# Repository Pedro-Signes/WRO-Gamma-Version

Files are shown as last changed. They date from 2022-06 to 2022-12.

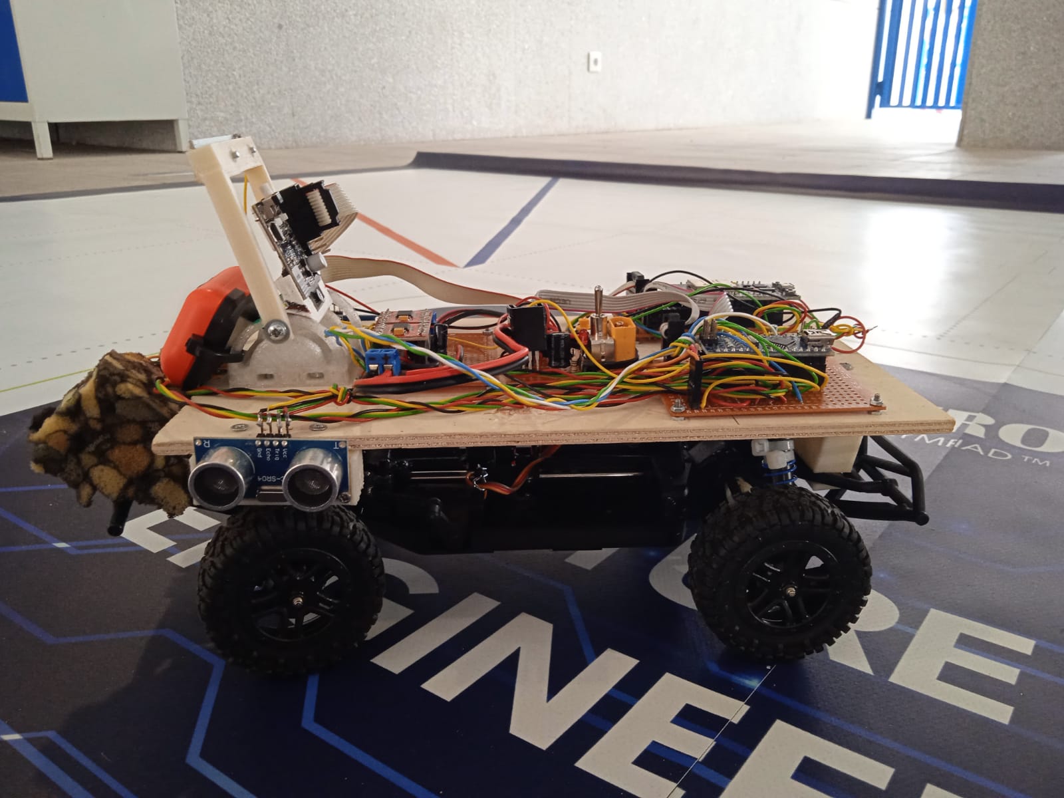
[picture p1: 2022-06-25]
vehicle-photos/FotoCocheIzquierda.jpeg

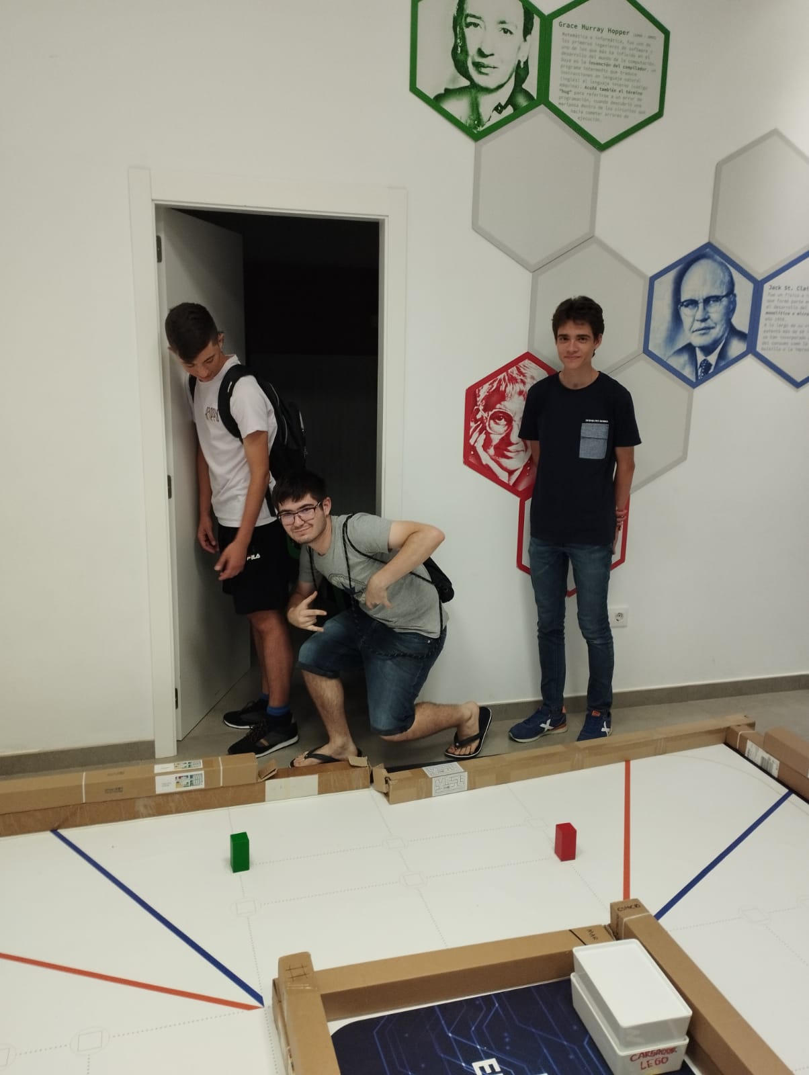
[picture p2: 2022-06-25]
team-photos/FotoGraciosa.jpeg

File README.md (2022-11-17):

# WRO-Gamma-Version
Diseño coche autónomo para la competición Future Engineers 2022
* Equipo: GammaVersion 
* Nombre del Coche: Mototruco
* Integrantes:
  * Javier Calero
  * Pablo Huertas
  * Pedro Signes

Nuestro equipo proviene de la cuidad de Denia (Alicante), y se compone de tres integrantes más un coach de la academia Diverbot, la cual también es la sede donde hacemos todas las pruebas con el robot.

A la hora de hablar del robot, tenemos que destacar los dos microcontroladores que tenemos, los cuales se comunican por un puerto I2C en un sistema maestro (ESP32) esclavo (Arduino Nano).No obstante nuestro robot contiene adicionalmente una cámara inteligente Pixy 2.0, la cual facilita mucho el trabajo a la hora de detectar los obstáculos y se comunica con el ESP32 mediante un puerto SPI.

Volviendo a los microcontroladores, el ESP32 a la hora de comunicarse con el Arduino Nano puede hacer dos cosas, preguntarle o ordenarle, puesto que el Arduino Nano es el esclavo de este sistema cuando reciba una de estas dos hará lo siguiente, responderá a la pregunta o hará la orden.

Metiéndonos más en detalle, el ESP32 contiene en su código una maquina de estados, la cual dependiendo de qué información reciba del Arduino Nano. No obstante, el ESP 32 no solo recibe información del Arduino Nano, también de la cámara, la cual al ser inteligente se puede programar para que nos mande un mensaje cuando vea un bloque, y de que color es.

Pasando al Arduino Nano, este está conectado al todo al motor, al servo, a los ultrasonidos, a un giroscopio, y a un encoder. Mientras esta esperando a los mensajes del ESP32 el Arduino Nano mantiene la brujula del coche funcionando y regula la velocidad a la indicada gracias a un DP programado.

Después cabe destacar la Pixy 2.0, la cual ya tiene un programa para detectar objetos y sus colores. No obstante, la cámara se le tiene que indicar unos parámetros en forma de asignaciones, que luego recibirá el ESP32 y con ellas puede tomar las decisiones. 

Por ultimo cabe destacar los cuatro ultrasonidos que posee el robot, ya que estos le indica la distancia que tiene delante, a los lados, y detrás. Esto datos llegaran al ESP32 mediante el sistema explicado previamente, y con ellos el ESP32 tomara diferentes decisiones.

Versión en Inglés/English Version

Autonomous car design for the Future Engineers competition 2022

* Team: GammaVersion 
* Name of the car: Mototruco
* Members:
  * Javier Calero
  * Pablo Huertas
  * Pedro Signes

Our team comes from the city of Denia (Valencian region, Spain), and the team is made up of three members (Pablo, Pedro & Javi) plus a coach from the Diverbot academy, which is also the headquarters where we do all the developement of the project. We met on February of this year and we have been working hard since then to succeed in accomplish the chellenge of the Future Engineers Category of the World Robot Olympiad 2022.

The base of our robot is the chassis of a radio control car that we have broke down. Therefore, we alredy have a structure, an engine and a servo-direction. To achieve the car being autonomous we have to add a microcontroller, for this job we decided at the begining to use a Arduino Uno. This has been changed in june to an ESP32 and an Arduino Nano because only one microcontroller was not enough to opperate all the program with the adequate accuracy. This paradigma has been used in the Madrid competition and in the national final, but two weeks ago we ran away of interrupt pins, so we added an Arduino Nano Every since all its pins have interruptions. To support these three microcontrollers we have designed a wooden plank, where later we would place all the electronics. To join the plank with the chassis we have designed a couple of 3D supports, a frontal wall and two lateral pillars.

Our car is divided in four parts: the structure, explained before; the microcontrollers, which run the program; the sensors and the engine and servos.
The main part of our robot is the three controllers each one with a different program running. These programs are not parallel or isolated, they communicate trough an I2C bus. This protocol consists on a master, who can ruequest or send data to a slave who obeys the orders of the master. In our case, the ESP32 is the master, and the Arduino Nano and the Arduino Nano Every are the slaves.

By using this protocol we enable the ESP32 to run the main program at a good pace. The ESP32 has a little state machine, which time ago was huge but we have been able to simplify it by the algorithm we have developed, which is going to be explained now. The function of the main program is to detect the color blocks and pass them by the correct side. The way we have done it is by calculating the position of the car, x and y coordinates (width and length, respectively), at every time and telling the car to go to certain X position, which will be right or left. The knowledge of the position can be achieved by integrating the distance and the angle of the car at every time with a certain trigonometric function. An encoder is used to know the position and an MPU 9250 to work out the angle. The encoder has been designed with the 3D printer with 8 holes to let the light pass trough and it has been connected to the Arduino Nano. The MPU has a gyroscope mode, which lets you know the angular speed of the car, and integrating the angular speed over time you calculate the angle at which the car is respect to the origin. Let us point that the MPU is also connected to the ESP32 by a I2C bus, but in a different port to the employed with the arduinos because it caused problems.

In reference to the algorithm to manage the car going to a specific coordinate, it is based in a PID controller, however only the P and D terms. The desired setpoint is the objective position, the variable to control is the position and the actuator is the direction servo. The error between the desired setpoint and the actual value of the variable is worked out and the proportional and derivative are aplied. The result of the calculations is the angle at which the car has to point to arrive to the desired position.

To keep the algorithm symetric in every section we reset the coordinate system, hence, to avoid a red block the car will always have to move 20 cm from the origin, the center of the section. This change of coordinates can be done by a simple mathematical opertaion or taking into account the distance to the walls.

Restarting the coordinate system and employing the PD controller of the position the turns are consequently genereated, because when the coordiante system changes the car will still try to be at the desired X coordinate and in order to magange this it will move the servo and turn. The only thing we have to do is to set at which position it has to start to turn.

Moving on to the Arduino Nano, it is connected to the whole motor, servo, ultrasonics, and encoder. While it is waiting for messages from ESP32 the Arduino uno keeps the car in the last indicated speed thanks to a programmed DP.

Then it is worth highlighting the Pixy 2.0, an intelligent Pixy 2.0 camera, which greatly facilitates the work when detecting obstacles. Pixy already has a software to detect objects and their colors. To return the data, the camera has to be configured in the form of assignments, which the ESP32 will then receive and with them it can make decisions.

Finally, it is worth mentioning the four ultrasounds that the robot poses, since these indicate the distance that it has in front, to the sides, and behind. This sensors are connected to the Arduino Nano but the data will reach the ESP32 through the system explained previously, and with it the ESP32 will make different decisions. Recently we have noticed that the ultrasonic sensors would not obtain enough accurate measures of the distance and this affects our program beacause we cannot have an accurate check of the position of the car. Therefore we decided to add new sensors, the TOF sensors or unofficialy laser sensors. These ones are connected to the Arduino Nano Every because as explained before, all the pins in this microcontroller have interruptions which allow us to measure better with this sensors.

This is all our car, which we have developed with hard work and effort, but learning a lot.

FotoEquipo

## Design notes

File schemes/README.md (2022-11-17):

The schematics of the electromechanical components are in the electronics folder.

Aquí está el esquema de los componentes electromecánicos que han sido usados en el vehículo y de cómo se conectan entre ellos.

El esquemaico actual es el Circuito 2.1.

The current schematic is Circuito 2.1.

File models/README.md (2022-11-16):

In this folder the 3D models used in our project can be found.

En esta carpeta tiene los modelos usados para imprimir las piezas en la imporesora 3D.

Los modelos están diseñados e Freecad, herramienra libre para diseño 3D, en las carpetas de los diferentes diseños se encuentran los archivos de edición de dicho programa, para visualizar los modelos, dentro de las carpetas "stl" se encuentran los ficheros .stl.

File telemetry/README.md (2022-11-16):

This folder may be neglected since it only contains a record of the telemetry data of some tests we have done.
The Wifi_reader file is an old python program to receive the data the ESP32 sent via Wifi.

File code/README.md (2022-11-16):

All the code used in our project is stored in this folder.

En esta carpeta se encuentra todo el código usado en el proyecto.

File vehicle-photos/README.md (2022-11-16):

In this folder you may find two car photos's folders.
The New Car folder is that of the new version of the car, which will be used in the International Final.

En esta carpeta se encuentran las 6 fotos de las 6 caras del coche.

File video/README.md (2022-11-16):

The folder New Url contains the url to the updated version of the car review video on YouTube. (16/11/2022)
The Old Url is obsolete since it shows an older version of the car.

En este directorio está el archivo que contiene el link al video que muestra el coche conduciendo de manera autónoma.

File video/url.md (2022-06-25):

URL al video de Youtube del coche moviendose de forma autónoma
https://youtu.be/MbsSwNEmdMk

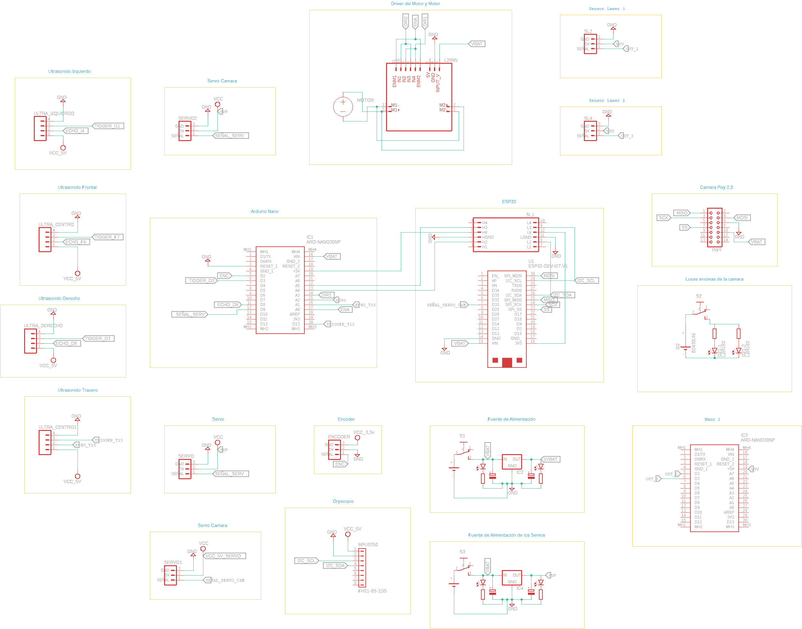
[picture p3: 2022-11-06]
schemes/electronics/Circuito/Circuito.png

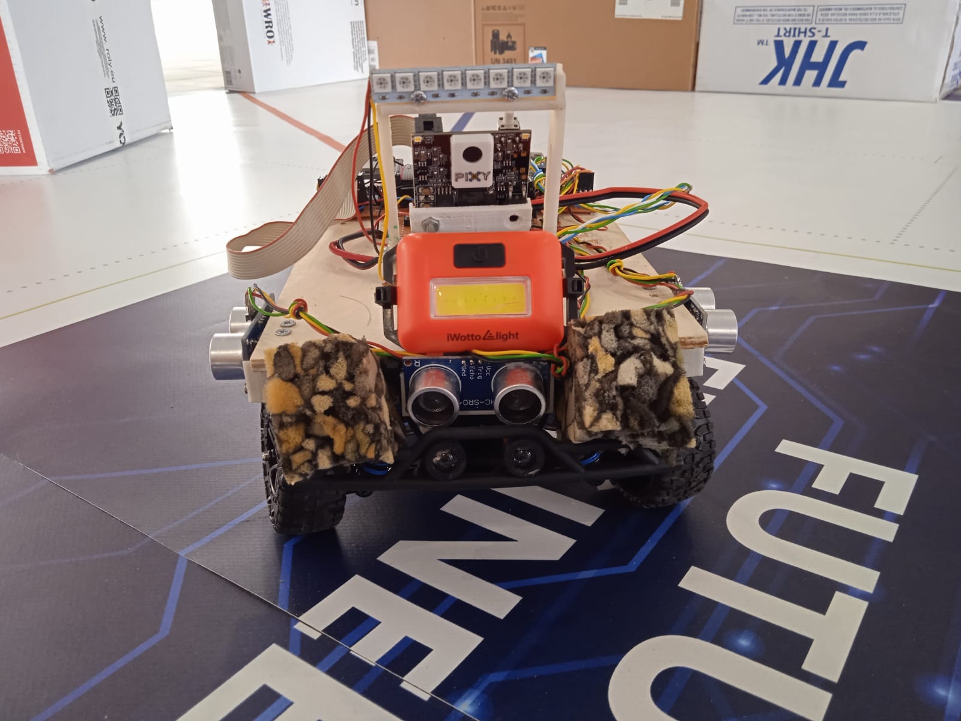
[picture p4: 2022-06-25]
vehicle-photos/FotoCocheDelante.jpeg

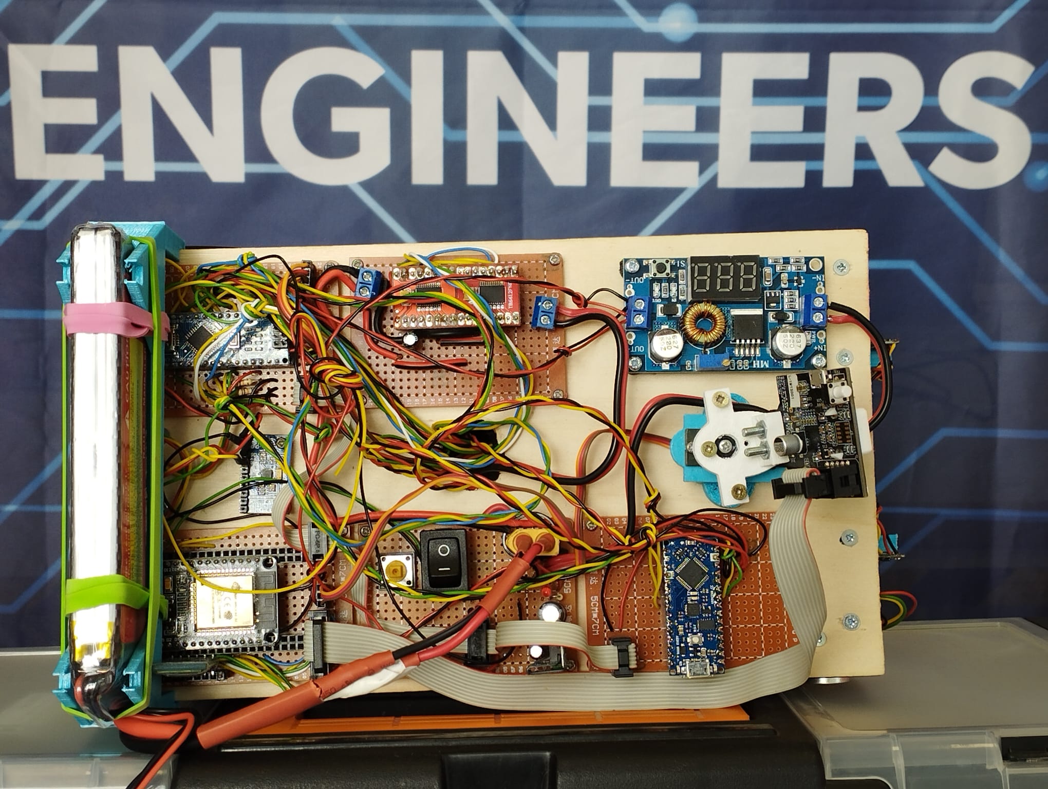
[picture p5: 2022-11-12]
vehicle-photos/New Car/FotoCocheArriba.jpg.jpeg

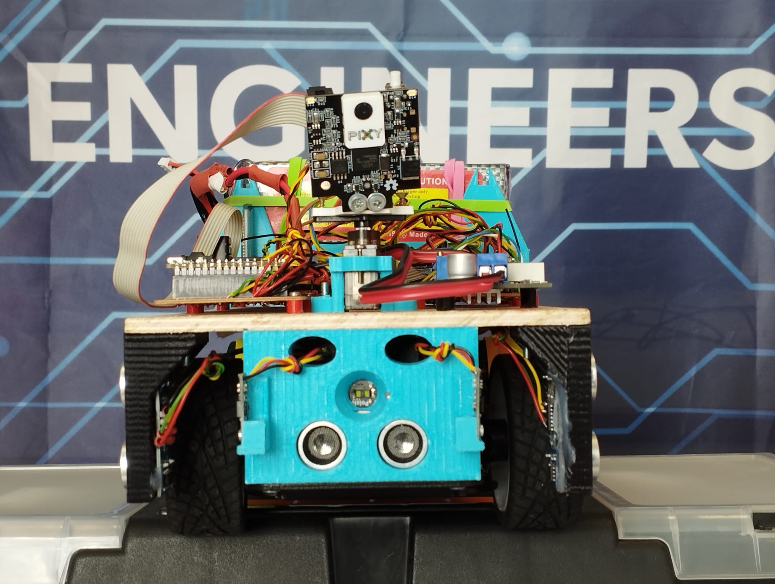
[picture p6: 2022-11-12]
vehicle-photos/New Car/FotoCocheDelante.jpg.jpeg

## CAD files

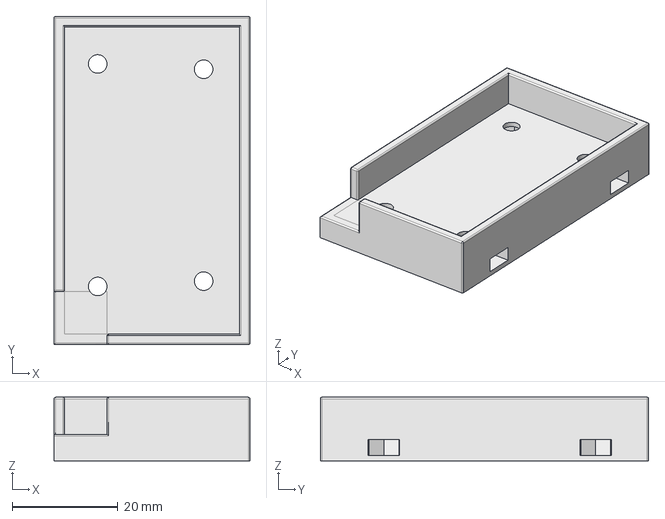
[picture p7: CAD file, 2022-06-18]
models/Soporte bateria/Soporte Bateria.FCStd
37.0 x 62.0 x 12.0 mm

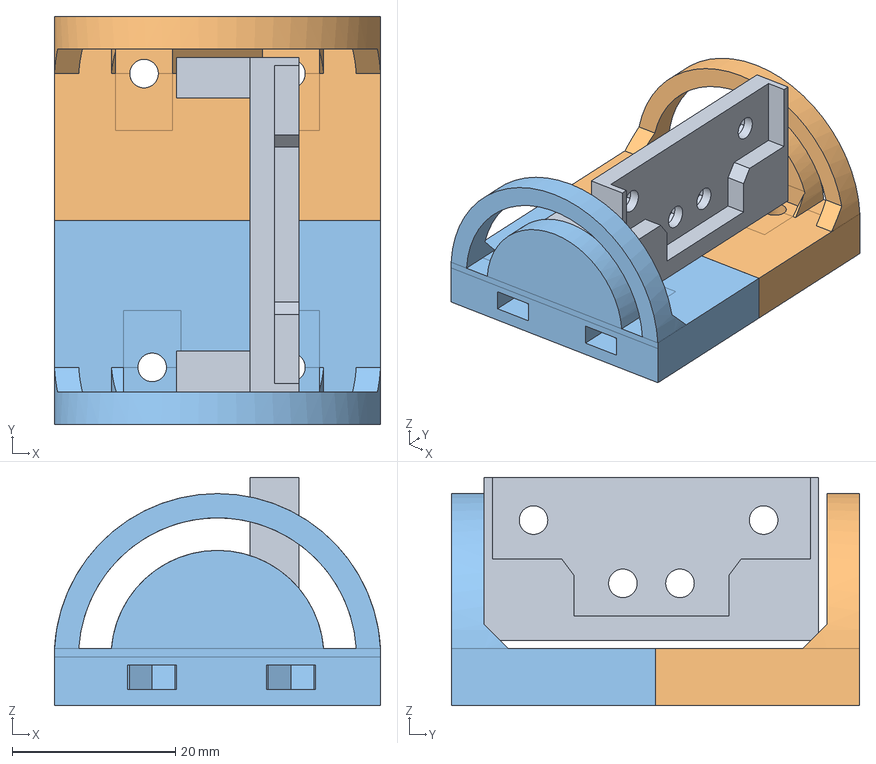
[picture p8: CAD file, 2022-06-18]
models/Soporte Camara/Soporte camara.FCStd
40.0 x 50.0 x 28.0 mm

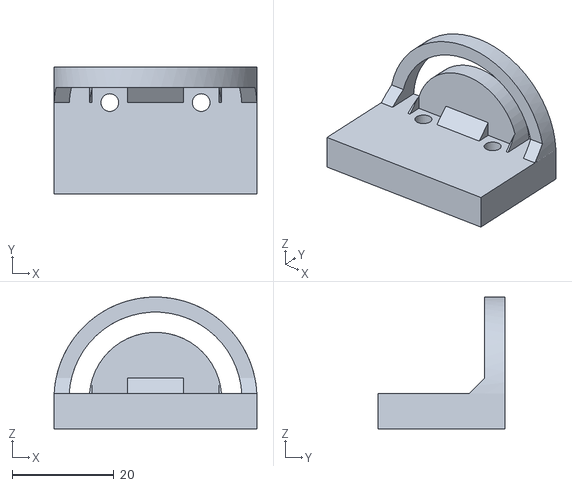
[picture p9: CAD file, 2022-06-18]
models/Soporte Camara/stl/Soporte camara 1.0/Soporte camara-Base1.stl
40.0 x 25.0 x 26.0

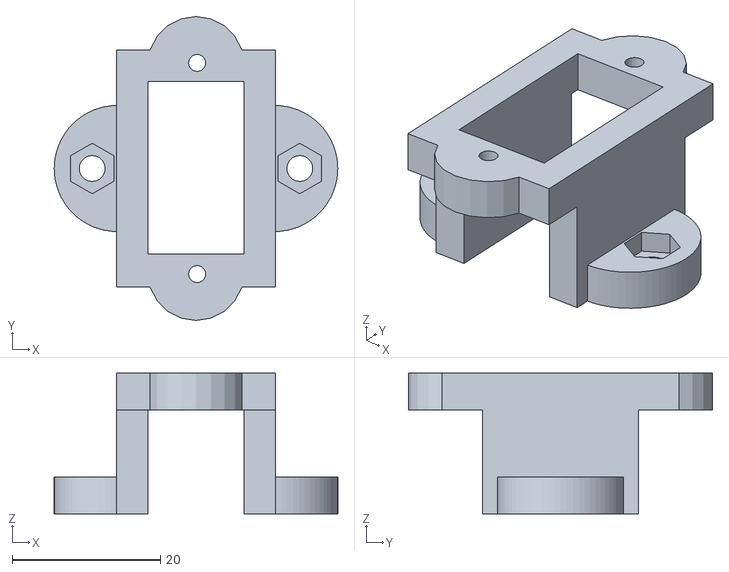
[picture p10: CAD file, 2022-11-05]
models/Soporte Camara/stl/Soporte camara 2.0/Soporte camara - Base servo.stl
38.2 x 41.0 x 19.0

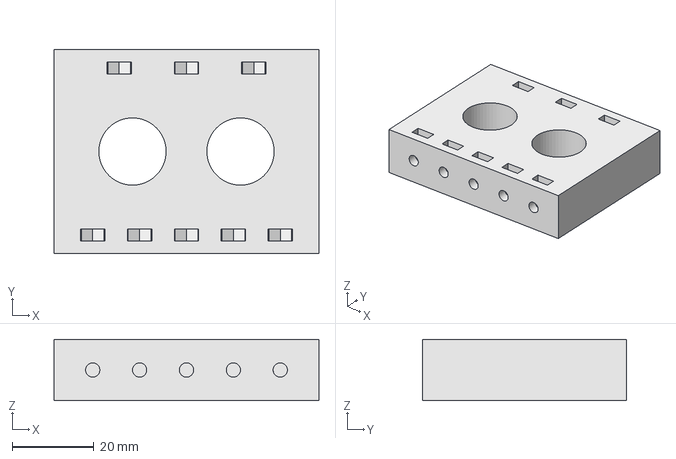
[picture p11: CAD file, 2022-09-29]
models/Soporte Delantero/Soporte delantero.FCStd
65.0 x 50.0 x 15.0 mm

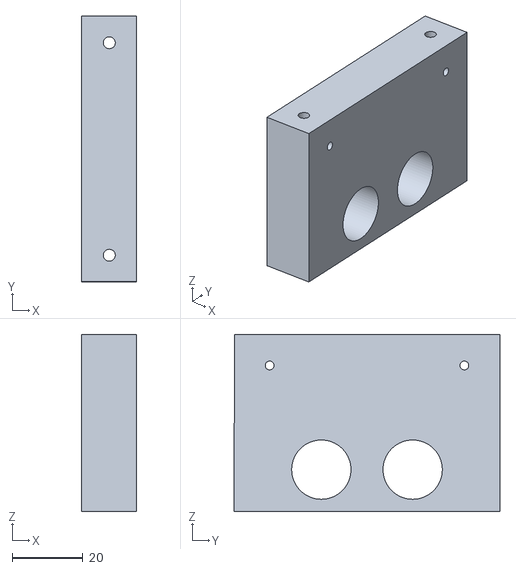
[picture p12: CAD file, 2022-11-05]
models/Soporte Delantero/stl/Soporte delantero 1.2/Soporte Frontal.stl
15.5 x 75.0 x 50.0

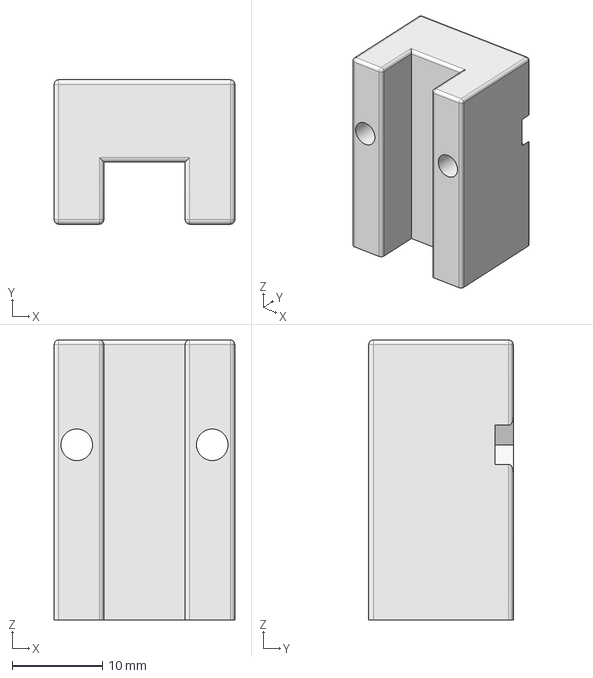
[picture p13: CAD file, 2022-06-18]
models/Soporte encoder/Soporte sensor vueltas.FCStd
20.0 x 16.0 x 31.0 mm

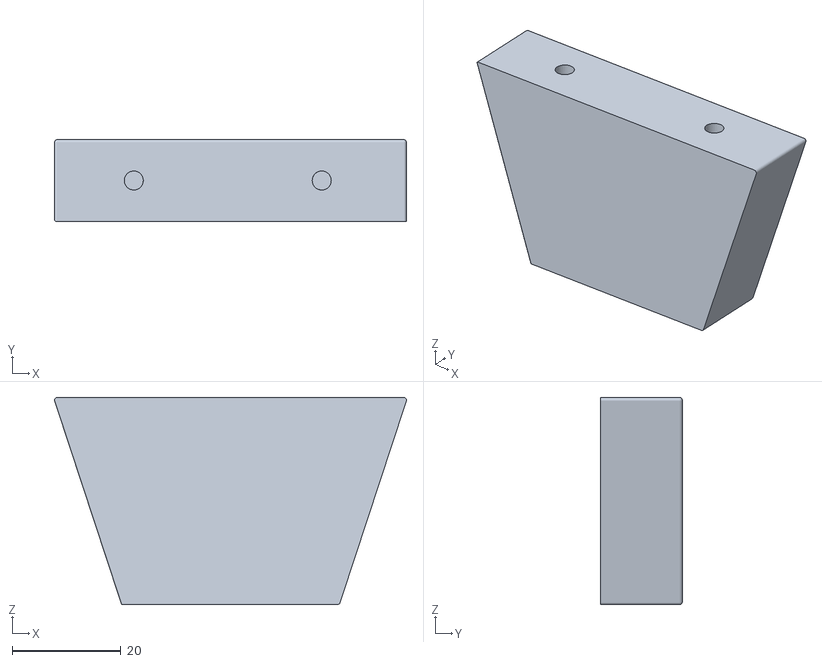
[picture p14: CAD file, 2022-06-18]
models/Soporte trasero/stl/Sujetador trasero-Fillet002.stl
64.6 x 15.0 x 38.0

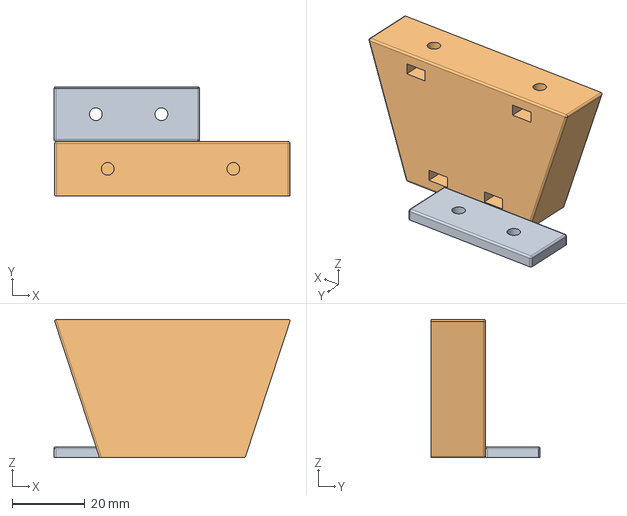
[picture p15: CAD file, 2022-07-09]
models/Soporte trasero/Sujetador trasero.FCStd
64.8 x 30.0 x 38.0 mm

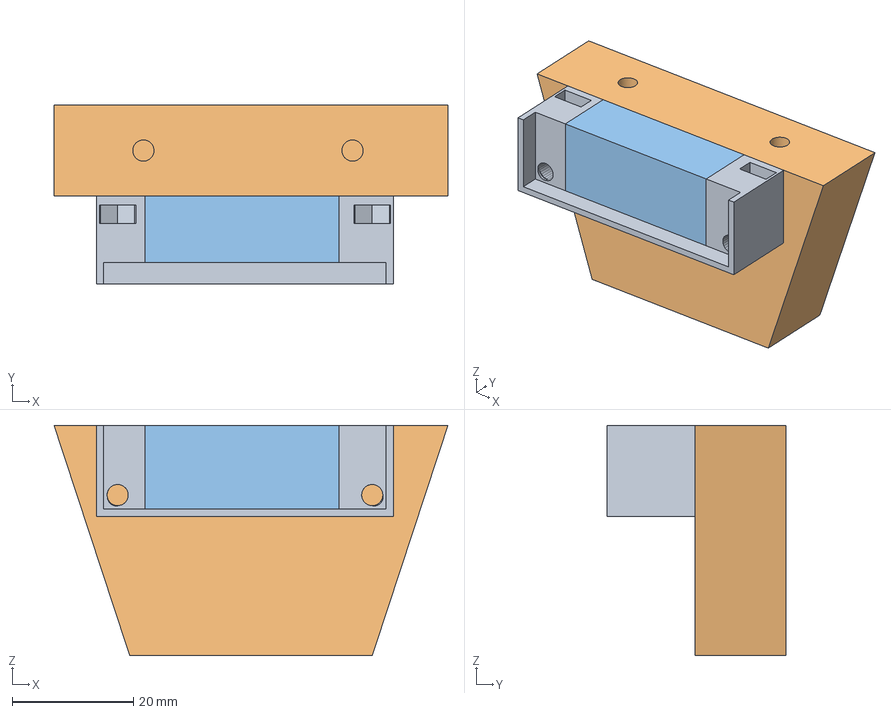
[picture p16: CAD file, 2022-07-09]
models/Soporte trasero2.0/Soporte.FCStd
65.0 x 29.5 x 38.0 mm
Soporte_Ultrasonidos001001001
Cubo

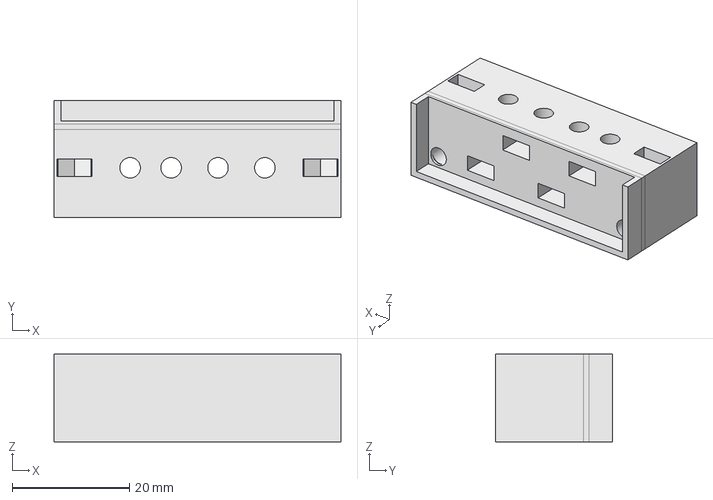
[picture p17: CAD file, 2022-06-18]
models/Soporte Ultrasonidos1.0/Soporte Ultrasonidos.FCStd
49.0 x 20.0 x 15.0 mm

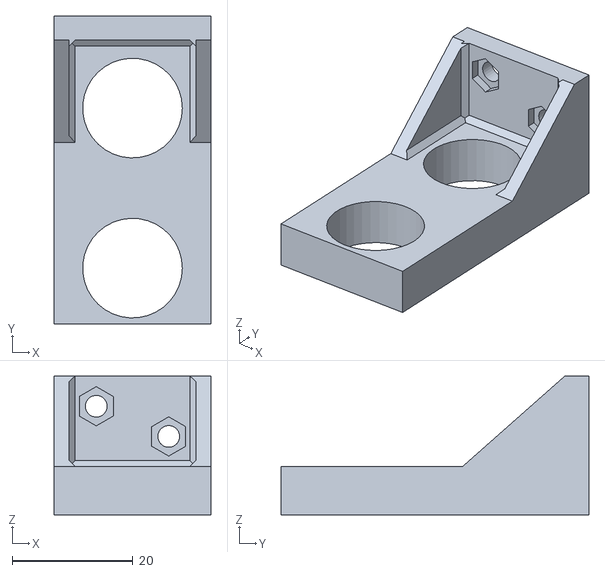
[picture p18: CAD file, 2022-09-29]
models/Soporte Ultrasonidos2.0/stl/Soporte ultrasonidos-Chamfer002.stl
26.0 x 51.0 x 23.0

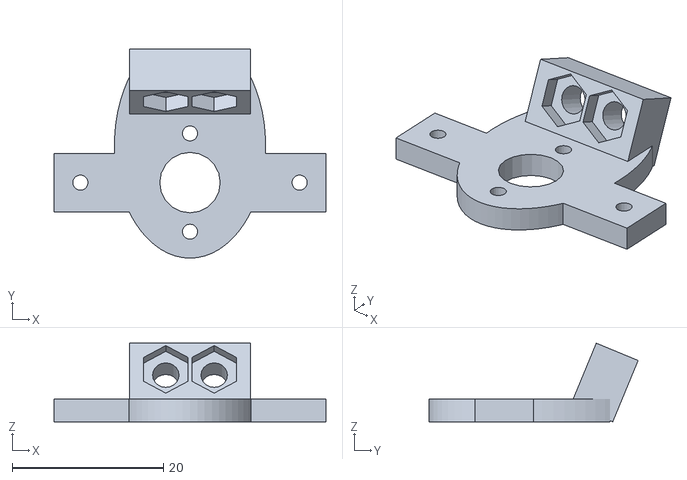
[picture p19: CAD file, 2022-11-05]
models/Soporte Camara/stl/Soporte camara 2.0/Soporte camara - Camara_1.stl
36.0 x 27.7 x 10.4

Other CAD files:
models/Soporte bateria/stl/Soporte Bateria-Fillet001.stl
models/Soporte Delantero/stl/Soporte delantero 1.0/Soporte delantero-Cut002.stl
models/Soporte encoder/stl/Soporte sensor.stl
models/Soporte Camara/stl/Soporte camara 1.0/Soporte camara-Base2.stl
models/Soporte Delantero/stl/Soporte delantero 1.0/Soporte delantero-Cut002Tumbado.stl
models/Soporte Camara/stl/Basura/Soporte camara-Base.stl
models/Soporte Camara/stl/Basura/Soporte camara-Base2.stl
models/Soporte Camara/stl/Basura/Soporte camara-Camara.stl
models/Soporte Camara/stl/Soporte camara 1.0/Soporte camara-Base.stl
models/Soporte Camara/stl/Soporte camara 1.0/Soporte camara-Camara.stl
models/Soporte Camara/stl/Soporte camara 2.0/Soporte camara - Camara_2.stl
models/Soporte Ultrasonidos1.0/stl/Soporte Ultrasonidos.stl
models/Soporte Ultrasonidos2.0/Soporte ultrasonidos.FCStd
models/Soporte encoder/stl/Soporte encoder -1mm.stl
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

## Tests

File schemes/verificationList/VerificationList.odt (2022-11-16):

Cosas a verificar

Cables conectados
Ruedas limpias
Ruedas infladas
Pixy calibrada: Bloques definidos Lineas detectadas Reconocimiento de los bloques Detección exclusiva (Solo lo que queremos) Ajustar inclinación pixy Ajustar altura pixy con tornillo
MPU calibrado
Batería cargada
Programa del Arduino Nano cargado
Programa del ESP32 cargado
Luz frontal cargada
Ultrasonidos calibrados
Ultrasonidos intactos
Servo funcionando No se calienta
Drivers funcionando No se calientan
Motor no se calienta
Botón funcionando
Indicador de voltaje funcionando
Esponjas en su lugar
El numero de vueltas está bien
Las signatures están bien
Calibrar Servo
El coche está bien colocado en medio
Comprobar fin del muro (ultrasonidos)
Quitar la telemetria

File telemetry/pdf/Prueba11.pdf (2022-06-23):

Hoja1

Página

b'169 | 20 | 20 | 0
5 | 90 -0.00
b'169 | 20 | 20 | 0
5 | 90 0.03
b'169 | 20 | 20 | 8
5 | 90 0.11
b'169 | 20 | 20 | 20
5 | 90 0.27
b'169 | 20 | 20 | 30
5 | 90 0.28
b'166 | 20 | 20 | 41
5 | 90 0.33
b'165 | 20 | 20 | 41
5 | 90 0.55
b'165 | 20 | 20 | 55
5 | 90 0.71
b'163 | 21 | 20 | 74
5 | 90 0.86
b'161 | 20 | 20 | 91
5 | 90 0.96
b'161 | 20 | 20 | 111
5 | 90 1.07
b'157 | 21 | 20 | 111
5 | 90 1.29
b'155 | 21 | 20 | 131
5 | 90 1.41
b'155 | 21 | 20 | 149
5 | 90 1.38
b'152 | 21 | 20 | 164
5 | 90 1.20
b'150 | 20 | 20 | 187
5 | 90 1.01
b'149 | 20 | 20 | 187
5 | 90 0.97
b'145 | 20 | 20 | 208
5 | 90 0.97
b'143 | 20 | 20 | 225
5 | 90 0.90
b'140 | 20 | 20 | 245
5 | 90 0.83
b'140 | 20 | 20 | 263
5 | 90 0.83
b'137 | 21 | 21 | 263
5 | 90 0.81
b'135 | 21 | 21 | 283
5 | 90 0.78
b'131 | 21 | 20 | 301
5 | 90 0.59
b'131 | 21 | 20 | 321
5 | 90 0.50
b'127 | 21 | 21 | 340
5 | 90 0.53
b'125 | 21 | 20 | 340
5 | 90 0.53
b'121 | 21 | 21 | 358
5 | 90 0.55
b'121 | 21 | 21 | 383
5 | 90 0.60
b'115 | 20 | 21 | 407
5 | 90 0.64
b'112 | 20 | 21 | 427
5 | 90 0.52
b'110 | 21 | 20 | 427
5 | 90 0.47
b'106 | 21 | 20 | 448
5 | 90 0.55
b'106 | 21 | 21 | 470
5 | 90 0.57
b'105 | 21 | 21 | 497
5 | 90 0.60
b'97 | 21 | 26 | 516
5 | 90 0.63
b'96 | 21 | 28 | 516
5 | 90 0.62
b'96 | 21 | 28 | 542
5 | 90 0.48
b'93 | 23 | 30 | 566
5 | 90 0.40
b'89 | 22 | 36 | 595
4 | 90 0.42
b'87 | 22 | 37 | 614
4 | 90 0.43
b'81 | 21 | 39 | 614
4 | 90 0.51
b'81 | 22 | 41 | 627
4 | 90 0.61
b'78 | 22 | 43 | 647
4 | 90 0.68
b'76 | 23 | 178 | 666
2 | 180 0.84
b'75 | 23 | 178 | 681
2 | 180 1.01
b'72 | 23 | 178 | 681
2 | 180 1.21
b'72 | 22 | 178 | 700
2 | 180 1.87
b'70 | 23 | 4 | 718
2 | 180 3.20
b'68 | 23 | 178 | 732
2 | 180 4.80
b'66 | 23 | 178 | 746
2 | 180 6.21
b'66 | 24 | 163 | 746
2 | 180 7.47
b'64 | 25 | 178 | 761
2 | 180 8.82

b'64 | 26 | 163 | 771
2 | 180 10.10
b'62 | 27 | 178 | 784
2 | 180 11.37
b'61 | 27 | 178 | 797
2 | 180 12.45
b'61 | 27 | 164 | 797
2 | 180 13.72
b'61 | 29 | 178 | 812
2 | 180 14.93
b'60 | 30 | 163 | 825
2 | 180 16.23
b'59 | 31 | 178 | 838
2 | 180 17.50
b'58 | 31 | 178 | 851
2 | 180 18.93
b'58 | 31 | 163 | 851
2 | 180 20.16
b'57 | 34 | 178 | 865
2 | 180 21.42
b'56 | 34 | 178 | 878
2 | 180 22.57
b'55 | 35 | 178 | 891
2 | 180 23.82
b'55 | 178 | 178 | 902
2 | 180 25.08
b'54 | 178 | 20 | 902
2 | 180 26.35
b'54 | 178 | 20 | 917
2 | 180 27.62
b'54 | 178 | 178 | 929
2 | 180 28.87
b'52 | 178 | 22 | 938
2 | 180 29.93
b'50 | 178 | 178 | 955
2 | 180 30.92
b'50 | 178 | 178 | 955
2 | 180 32.09
b'50 | 178 | 23 | 968
2 | 180 33.22
b'48 | 178 | 23 | 980
2 | 180 34.48
b'48 | 64 | 178 | 990
2 | 180 35.75
b'178 | 65 | 140 | 1005
2 | 180 36.96
b'178 | 65 | 79 | 1005
2 | 180 38.07
b'178 | 65 | 79 | 1019
2 | 180 39.31
b'178 | 178 | 178 | 1033
2 | 180 40.57
b'178 | 178 | 178 | 1047
2 | 180 41.91
b'178 | 66 | 0 | 1059
2 | 180 43.38
b'178 | 67 | 178 | 1059
2 | 180 44.72
b'178 | 67 | 7 | 1072
2 | 180 45.99
b'178 | 68 | 7 | 1086
2 | 180 47.17
b'178 | 68 | 57 | 1097
2 | 180 48.44
b'178 | 68 | 57 | 1110
2 | 180 49.56
b'178 | 68 | 57 | 1110
2 | 180 50.60
b'178 | 69 | 57 | 1123
2 | 180 51.71
b'178 | 72 | 72 | 1137
2 | 180 52.83
b'178 | 72 | 72 | 1149
2 | 180 54.01
b'178 | 74 | 57 | 1160
2 | 180 55.32
b'177 | 74 | 55 | 1160
2 | 180 56.45
b'173 | 178 | 55 | 1175
2 | 180 57.64
b'173 | 112 | 55 | 1188
2 | 180 58.79
b'173 | 109 | 56 | 1197
2 | 180 59.92
b'173 | 109 | 56 | 1211
2 | 180 61.11
b'171 | 110 | 55 | 1211
2 | 180 62.42
b'171 | 110 | 55 | 1225
2 | 180 63.60
b'167 | 110 | 54 | 1237
2 | 180 64.89
b'167 | 178 | 54 | 1251
2 | 180 66.06
b'167 | 178 | 54 | 1261
2 | 180 67.22
b'167 | 178 | 54 | 1261
2 | 180 68.24
b'165 | 178 | 54 | 1273
2 | 180 69.18
b'165 | 178 | 54 | 1288
2 | 180 70.37
b'163 | 32 | 54 | 1300
2 | 180 71.51
b'163 | 32 | 54 | 1311
2 | 180 72.58

b'178 | 135 | 55 | 1311
2 | 180 73.70
b'178 | 135 | 55 | 1323
2 | 180 74.75
b'178 | 32 | 54 | 1333
2 | 180 75.87
b'178 | 32 | 54 | 1349
2 | 180 77.04
b'178 | 33 | 53 | 1361
2 | 180 78.23
b'178 | 33 | 53 | 1361
2 | 180 79.43
b'178 | 32 | 53 | 1373
2 | 180 80.63
b'178 | 32 | 53 | 1383
2 | 180 81.79
b'178 | 32 | 53 | 1398
2 | 180 82.88
b'178 | 33 | 53 | 1410
2 | 180 83.96
b'178 | 31 | 52 | 1410
2 | 180 84.85
b'178 | 32 | 53 | 1423
2 | 180 85.64
b'178 | 32 | 53 | -2
0 | 180 86.43
b'178 | 32 | 53 | 11
0 | 180 87.13
b'178 | 32 | 53 | 30
0 | 180 87.77
b'178 | 32 | 53 | 30
0 | 180 88.62
b'178 | 32 | 52 | 51
0 | 180 89.59
b'178 | 32 | 52 | 71
0 | 180 90.73
b'178 | 32 | 52 | 91
0 | 180 91.88
b'178 | 33 | 52 | 117
0 | 180 93.11
b'178 | 33 | 51 | 117
0 | 180 93.93
b'178 | 33 | 51 | 142
0 | 180 94.15
b'178 | 34 | 52 | 168
0 | 180 94.04
b'178 | 34 | 50 | 193
0 | 180 93.68
b'178 | 35 | 50 | 193
0 | 180 93.01
b'175 | 35 | 50 | 227
0 | 180 92.18
b'175 | 36 | 50 | 255
0 | 180 91.33
b'170 | 36 | 51 | 283
0 | 180 90.67
b'164 | 35 | 50 | 313
0 | 180 90.14
b'161 | 34 | 51 | 313
0 | 180 89.94
b'153 | 34 | 51 | 345
0 | 180 90.00
b'153 | 34 | 51 | 376
0 | 180 90.32
b'146 | 34 | 51 | 407
0 | 180 90.65
b'140 | 34 | 51 | 438
0 | 180 91.03
b'134 | 34 | 50 | 438
0 | 180 91.37
b'128 | 34 | 50 | 473
1 | 180 91.63
b'122 | 34 | 50 | 508
1 | 180 91.75
b'122 | 35 | 49 | 533
1 | 180 91.81
b'117 | 36 | 49 | 558
1 | 180 92.05
b'113 | 36 | 49 | 558
1 | 180 92.06
b'106 | 35 | 49 | 584
1 | 180 91.78
b'103 | 35 | 50 | 611
1 | 180 91.55
b'100 | 35 | 51 | 639
1 | 180 91.27
b'100 | 35 | 51 | 661
1 | 180 90.98
b'95 | 35 | 52 | 661
1 | 180 90.89
b'91 | 35 | 53 | 686
1 | 180 90.66
b'85 | 36 | 56 | 706
4 | 180 90.43
b'85 | 36 | 64 | 726
4 | 180 90.48
b'81 | 35 | 66 | 744
4 | 180 90.47
b'80 | 35 | 66 | 744
4 | 180 90.47
b'76 | 35 | 66 | 766
4 | 180 90.49
b'76 | 35 | 178 | 786
2 | 270 90.57
b'74 | 35 | 178 | 802
2 | 270 90.60

b'70 | 36 | 147 | 822
2 | 270 90.76
b'68 | 36 | 147 | 822
2 | 270 91.51
b'68 | 36 | 178 | 841
2 | 270 92.88
b'66 | 37 | 151 | 858
2 | 270 94.58
b'64 | 38 | 178 | 874
2 | 270 96.16
b'63 | 40 | 152 | 888
2 | 270 97.58
b'62 | 40 | 152 | 888
2 | 270 98.94
b'62 | 40 | 178 | 907
2 | 270 100.32
b'60 | 40 | 152 | 922
2 | 270 101.63
b'58 | 40 | 152 | 935
2 | 270 102.94
b'57 | 42 | 154 | 949
2 | 270 104.35
b'57 | 42 | 154 | 949
2 | 270 105.67
b'57 | 43 | 178 | 965
2 | 270 107.09
b'56 | 44 | 153 | 979
2 | 270 108.31
b'55 | 44 | 153 | 992
2 | 270 109.52
b'55 | 46 | 178 | 1005
2 | 270 110.73
b'53 | 48 | 153 | 1005
2 | 270 112.06
b'52 | 48 | 178 | 1018
2 | 270 113.20
b'50 | 178 | 23 | 1035
2 | 270 114.47
b'50 | 178 | 23 | 1049
2 | 270 115.76
b'49 | 178 | 83 | 1061
2 | 270 117.10
b'48 | 143 | 83 | 1061
2 | 270 118.24
b'48 | 142 | 81 | 1075
2 | 270 119.30
b'48 | 140 | 81 | 1088
2 | 270 120.49
b'46 | 142 | 80 | 1101
2 | 270 121.74
b'46 | 142 | 80 | 1113
2 | 270 122.90
b'46 | 140 | 178 | 1113
2 | 270 124.02
b'44 | 126 | 68 | 1128
2 | 270 125.21
b'43 | 125 | 178 | 1140
2 | 270 126.43
b'44 | 125 | 83 | 1153
2 | 270 127.55
b'44 | 127 | 83 | 1164
2 | 270 128.71
b'43 | 74 | 79 | 1164
2 | 270 129.83
b'43 | 130 | 80 | 1177
2 | 270 131.01
b'43 | 130 | 80 | 1186
2 | 270 132.28
b'178 | 143 | 178 | 1201
2 | 270 133.57
b'178 | 143 | 0 | 1216
2 | 270 134.87
b'178 | 145 | 0 | 1216
2 | 270 136.22
b'178 | 145 | 70 | 1231
2 | 270 137.55
b'178 | 146 | 70 | 1242
2 | 270 138.83
b'178 | 146 | 70 | 1253
2 | 270 140.23
b'178 | 148 | 73 | 1268
2 | 270 141.52
b'178 | 148 | 73 | 1268
2 | 270 142.86
b'167 | 148 | 178 | 1281
2 | 270 144.18
b'167 | 150 | 178 | 1295
2 | 270 145.54
b'162 | 150 | 0 | 1310
2 | 270 146.97
b'160 | 150 | 67 | 1323
2 | 270 148.27
b'160 | 153 | 67 | 1323
2 | 270 149.68
b'157 | 153 | 69 | 1335
2 | 270 150.93
b'157 | 178 | 69 | 1347
2 | 270 152.03
b'155 | 178 | 71 | 1361
2 | 270 153.11
b'155 | 178 | 71 | 1375
2 | 270 154.27
b'153 | 178 | 65 | 1375
2 | 270 155.35
b'153 | 178 | 67 | 1387
2 | 270 156.58

b'150 | 178 | 67 | 1398
2 | 270 157.70
b'150 | 178 | 64 | 1411
2 | 270 158.84
b'150 | 178 | 65 | 1423
2 | 270 159.89
b'150 | 178 | 65 | 1423
2 | 270 161.06
b'148 | 178 | 63 | 1434
2 | 270 162.13
b'178 | 178 | 62 | 1447
2 | 270 163.29
b'178 | 178 | 62 | 1459
2 | 270 164.55
b'178 | 178 | 62 | 1470
2 | 270 165.67
b'178 | 178 | 62 | 1470
2 | 270 166.84
b'143 | 178 | 61 | 1484
2 | 270 168.05
b'163 | 27 | 60 | 1499
2 | 270 169.29
b'161 | 27 | 60 | 1510
2 | 270 170.51
b'144 | 27 | 60 | 1524
2 | 270 171.66
b'144 | 27 | 60 | 1524
2 | 270 172.86
b'159 | 28 | 59 | 1535
2 | 270 173.93
b'158 | 28 | 59 | 1545
2 | 270 174.94
b'178 | 28 | 59 | 1560
2 | 270 175.81
b'178 | 28 | 59 | 4
0 | 270 176.55
b'178 | 27 | 59 | 4
0 | 270 177.21
b'178 | 28 | 60 | 23
0 | 270 177.96
b'178 | 28 | 60 | 45
0 | 270 178.93
b'178 | 28 | 61 | 68
0 | 270 180.02
b'178 | 29 | 57 | 89
0 | 270 181.23
b'178 | 29 | 57 | 89
0 | 270 182.66
b'176 | 30 | 56 | 113
0 | 270 183.69
b'176 | 30 | 56 | 139
0 | 270 184.31
b'173 | 30 | 56 | 166
0 | 270 184.57
b'168 | 30 | 55 | 194
0 | 270 184.25
b'168 | 30 | 55 | 194
0 | 270 183.61
b'157 | 29 | 55 | 224
0 | 270 182.86
b'153 | 29 | 55 | 253
0 | 270 181.94
b'153 | 29 | 55 | 282
0 | 270 180.97
b'147 | 28 | 55 | 312
0 | 270 180.22
b'141 | 28 | 55 | 312
0 | 270 179.77
b'141 | 127 | 56 | 347
0 | 270 179.51
b'129 | 28 | 56 | 375
0 | 270 179.42
b'129 | 28 | 56 | 407
0 | 270 179.62
b'123 | 28 | 56 | 407
0 | 270 179.97
b'116 | 28 | 56 | 443
0 | 270 180.32
b'116 | 28 | 56 | 475
1 | 270 180.71
b'111 | 27 | 55 | 504
1 | 270 181.31
b'99 | 31 | 55 | 531
1 | 270 181.82
b'95 | 31 | 55 | 531
1 | 270 182.23
b'95 | 28 | 55 | 559
1 | 270 182.34
b'90 | 28 | 55 | 584
1 | 270 182.34
b'85 | 28 | 54 | 609
4 | 270 182.33
b'81 | 28 | 54 | 632
4 | 270 182.13
b'78 | 28 | 54 | 632
4 | 270 181.82
b'75 | 27 | 54 | 659
4 | 270 181.51
b'71 | 28 | 54 | 681
4 | 270 181.32
b'69 | 28 | 54 | 700
4 | 270 181.23
b'69 | 27 | 54 | 722
4 | 270 181.14
b'66 | 27 | 54 | 722
4 | 270 180.94

b'63 | 27 | 55 | 739
4 | 270 180.82
b'60 | 27 | 56 | 758
4 | 270 180.70
b'59 | 27 | 56 | 782
4 | 270 180.66
b'59 | 27 | 56 | 795
4 | 270 180.67
b'57 | 27 | 56 | 795
4 | 270 180.71
b'54 | 27 | 57 | 813
4 | 270 180.81
b'51 | 27 | 57 | 831
4 | 270 180.92
b'50 | 27 | 57 | 846
4 | 270 180.93
b'50 | 27 | 57 | 861
4 | 270 180.89
b'47 | 27 | 57 | 861
4 | 270 180.85
b'47 | 27 | 58 | 875
4 | 270 180.85
b'45 | 27 | 58 | 893
4 | 270 180.88
b'43 | 27 | 59 | 908
4 | 270 180.93
b'41 | 27 | 59 | 920
4 | 270 180.92
b'41 | 27 | 60 | 920
4 | 270 180.90
b'40 | 27 | 61 | 933
4 | 270 180.89
b'39 | 27 | 63 | 947
4 | 270 180.86
b'38 | 28 | 64 | 962
4 | 270 180.86
b'36 | 29 | 76 | 975
4 | 270 180.90
b'36 | 29 | 76 | 975
4 | 270 180.92
b'37 | 31 | 77 | 989
4 | 270 180.95
b'35 | 31 | 77 | 999
4 | 270 180.95
b'32 | 55 | 78 | 1014
4 | 270 180.95
b'31 | 55 | 78 | 1026
4 | 270 180.95
b'29 | 27 | 178 | 1026
2 | 360 180.95
b'28 | 27 | 178 | 1039
2 | 360 180.91
b'28 | 28 | 178 | 1052
2 | 360 181.16
b'26 | 28 | 178 | 1066
2 | 360 182.12
b'25 | 28 | 178 | 1077
2 | 360 183.30
b'25 | 28 | 178 | 1077
2 | 360 184.53
b'24 | 29 | 178 | 1090
2 | 360 185.64
b'21 | 29 | 178 | 1101
2 | 360 186.83
b'21 | 29 | 178 | 1114
2 | 360 188.01
b'20 | 30 | 178 | 1126
2 | 360 189.30
b'22 | 30 | 178 | 1126
2 | 360 190.45
b'22 | 30 | 178 | 1137
2 | 360 191.61
b'17 | 32 | 178 | 1153
2 | 360 192.70
b'17 | 33 | 178 | 1164
2 | 360 193.76
b'20 | 33 | 178 | 1173
2 | 360 194.94
b'16 | 33 | 178 | 1173
2 | 360 196.05
b'15 | 34 | 178 | 1186
2 | 360 197.02
b'178 | 34 | 178 | 1200
2 | 360 197.97
b'178 | 35 | 178 | 1212
2 | 360 198.95
b'12 | 36 | 178 | 1223
2 | 360 200.09
b'13 | 36 | 178 | 1223
2 | 360 201.18
b'13 | 37 | 178 | 1237
2 | 360 202.35
b'118 | 37 | 178 | 1248
2 | 360 203.57
b'178 | 40 | 78 | 1262
2 | 360 204.83
b'178 | 40 | 78 | 1272
2 | 360 206.07
b'178 | 40 | 78 | 1272
2 | 360 207.22
b'178 | 42 | 69 | 1284
2 | 360 208.23
b'178 | 42 | 69 | 1295
2 | 360 208.93
b'129 | 43 | 69 | 1301
2 | 360 208.75

b'178 | 44 | 70 | 1307
2 | 360 208.16
b'178 | 43 | 77 | 1307
2 | 360 208.10
b'7 | 45 | 78 | 1309
2 | 360 208.23
b'7 | 45 | 78 | 1317
2 | 360 208.09
b'178 | 44 | 178 | 1325
2 | 360 207.72
b'178 | 44 | 178 | 1329
2 | 360 207.34
b'178 | 44 | 0 | 1329
2 | 360 207.04
b'178 | 45 | 80 | 1335
2 | 360 206.62
b'178 | 45 | 79 | 1341
2 | 360 206.19
b'178 | 45 | 79 | 1350
2 | 360 205.68
b'178 | 44 | 78 | 1360
2 | 360 205.05
b'6 | 45 | 78 | 1360
2 | 360 204.41
b'6 | 44 | 79 | 1366
2 | 360 203.80
b'6 | 44 | 178 | 1374
2 | 360 203.29
b'5 | 45 | 3 | 1383
2 | 360 202.70
b'178 | 45 | 178 | 1393
2 | 360 202.08
b'178 | 44 | 178 | 1393
2 | 360 201.32
b'129 | 44 | 0 | 1400
2 | 360 200.77
b'124 | 45 | 178 | 1407
2 | 360 200.31
b'6 | 44 | 2 | 1419
2 | 360 199.92
b'6 | 45 | 178 | 1429
2 | 360 199.13
b'5 | 45 | 178 | 1429
2 | 360 198.23
b'5 | 46 | 178 | 1440
2 | 360 197.61
b'5 | 134 | 89 | 1448
2 | 360 197.05
b'5 | 45 | 178 | 1456
2 | 360 196.50
b'4 | 48 | 178 | 1466
2 | 360 195.80
b'5 | 48 | 178 | 1466
2 | 360 195.15
b'5 | 46 | 178 | 1476
2 | 360 194.44
b'119 | 92 | 87 | 1490
2 | 360 193.79
b'105 | 60 | 89 | 1500
2 | 360 193.43
b'119 | 88 | 88 | 1508
2 | 360 193.01
b'119 | 88 | 88 | 1508
2 | 360 192.61
b'104 | 91 | 178 | 1519
2 | 360 192.32
b'118 | 91 | 178 | 1530
2 | 360 192.05
b'118 | 87 | 42 | 1540
2 | 360 191.96
b'117 | 90 | 89 | 1549
2 | 360 192.07
b'116 | 92 | 121 | 1549
2 | 360 192.10
b'115 | 92 | 121 | 1563
2 | 360 192.07
b'115 | 89 | 120 | 1578
2 | 360 192.31
b'114 | 89 | 120 | 1592
2 | 360 192.73
b'114 | 91 | 120 | 1604
2 | 360 193.24
b'114 | 91 | 120 | 1604
2 | 360 193.54
b'113 | 94 | 121 | 1616
2 | 360 193.65
b'110 | 94 | 63 | 1629
2 | 360 193.84
b'110 | 147 | 63 | 1641
2 | 360 194.12
b'110 | 147 | 120 | 1651
2 | 360 194.35
b'6 | 92 | 178 | 1651
2 | 360 194.53
b'7 | 92 | 153 | 1663
2 | 360 194.68
b'7 | 91 | 153 | 1675
2 | 360 194.78
b'109 | 139 | 57 | 1686
2 | 360 195.01
b'115 | 139 | 57 | 1702
2 | 360 195.27
b'115 | 94 | 178 | 1702
2 | 360 195.69
b'5 | 92 | 42 | 1718
2 | 360 196.13

b'5 | 95 | 76 | 1729
2 | 360 196.63
b'6 | 95 | 178 | 1743
2 | 360 197.24
b'5 | 148 | 178 | 1755
2 | 360 197.92
b'5 | 140 | 99 | 1755
2 | 360 198.64
b'6 | 148 | 54 | 1770
2 | 360 199.30
b'5 | 148 | 178 | 1783
2 | 360 199.96
b'6 | 148 | 98 | 1796
2 | 360 200.45
b'5 | 148 | 98 | 1806
2 | 360 200.76
b'5 | 148 | 55 | 1806
2 | 360 201.10
b'5 | 148 | 178 | 1818
2 | 360 201.48
b'111 | 150 | 0 | 1831
2 | 360 201.88
b'111 | 93 | 73 | 1851
2 | 360 202.42
b'111 | 93 | 73 | 1851
2 | 360 202.66
b'111 | 151 | 178 | 1876
2 | 360 203.33
b'112 | 151 | 0 | 1888
2 | 360 203.70
b'5 | 151 | 96 | 1902
2 | 360 204.65
b'5 | 156 | 96 | 1916
2 | 360 205.15
b'7 | 156 | 178 | 1928
2 | 360 205.64
b'102 | 150 | 0 | 1940
2 | 360 206.15
b'102 | 151 | 0 | 1953
2 | 360 206.52
b'113 | 151 | 85 | 1953
2 | 360 206.73
b'111 | 151 | 85 | 1963
2 | 360 206.92
b'111 | 152 | 86 | 1972
2 | 360 207.18
b'123 | 152 | 86 | 1984
2 | 360 207.58
b'110 | 161 | 86 | 1998
2 | 360 207.95
b'110 | 151 | 178 | 1998
2 | 360 208.19
b'112 | 151 | 178 | 2010
2 | 360 208.48
b'112 | 157 | 0 | 2024
2 | 360 208.61
b'112 | 157 | 48 | 2037
2 | 360 208.73
b'112 | 158 | 48 | 2047
2 | 360 208.90
b'112 | 150 | 48 | 2047
2 | 360 208.96
b'112 | 151 | 49 | 2060
2 | 360 209.11
b'111 | 151 | 49 | 2071
2 | 360 209.29
b'111 | 150 | 178 | 2082
2 | 360 209.50
b'111 | 150 | 178 | 2094
2 | 360 209.72
b'111 | 151 | 0 | 2094
2 | 360 209.88
b'110 | 150 | 178 | 2108
2 | 360 209.92
b'113 | 150 | 0 | 2121
2 | 360 209.91
b'113 | 150 | 0 | 2128
2 | 360 209.90
b'110 | 150 | 178 | 2136
2 | 360 209.97
b'110 | 152 | 178 | 2136
2 | 360 210.09
b'111 | 152 | 0 | 2146
2 | 360 210.28
b'111 | 151 | 178 | 2160
2 | 360 210.38
b'111 | 150 | 178 | 2170
2 | 360 210.34
b'109 | 150 | 0 | 2180
2 | 360 210.21
b'109 | 151 | 0 | 2180
2 | 360 210.01
b'110 | 151 | 180 | 2187
2 | 360 209.65

0

0

0

0 0'
0

0

0

0 0'
8

0

0

0 0'
20

0

0

0 0'
30

0

0

0 0'
41

0

0

0 0'
41

0

0

0 0'
55

0

0

0 0'
74

0

0

0 0'
91

0

0

0 0'
111 | -2 | -2

0 0'
111 | -2 | -2

0 0'
131 | -2 | -2

0 0'
149 | -2 | -2

0 0'
164 | -2 | -2

0 0'
187 | -2 | -2

0 0'
187 | 0 | 0

0 0'
208 | 0 | 0

0 0'
225 | 0 | 0

0 0'
245 | 0 | 0

0 0'
263 | 0 | 0

0 0'
263 | 0 | 0

0 0'
283 | 0 | 0

0 0'
301 | 0 | 0

0 0'
321 | 0 | 0

0 0'
340 | 0 | 0

0 0'
340 | 0 | 0

0 0'
358 | 0 | 0

0 0'
383 | 0 | 0

0 0'
407 | 0 | 0

0 0'
427 | 0 | 0

0 0'
427 | 0 | 0

0 0'
448 | 0 | 0

0 0'
470 | 0 | 0

0 0'
497 | 0 | 0

0 0'
516 | 0 | 0

0 0'
516 | 0 | 0

0 0'
542 | 0 | 0

0 0'
566 | 0 | 0

0 0'
595 | 0 | 0

0 0'
614 | 0 | 0

0 0'
614 | 0 | 0

0 0'
627 | 0 | 0

0 0'
647 | 0 | 0

0 0'
666 | 127 | 127

1 1'
681 | 127 | 127

1 1'
681 | 127 | 127

1 1'
700 | 127 | 127

1 1'
718 | 127 | 127

1 1'
732 | 127 | 127

1 1'
746 | 127 | 127

1 1'
746 | 127 | 127

1 1'
761 | 127 | 127

1 1'

771 | 127 | 127

1 1'
784 | 127 | 127

1 1'
797 | 127 | 127

1 1'
797 | 127 | 127

1 1'
812 | 127 | 127

1 1'
825 | 127 | 127

1 1'
838 | 127 | 127

1 1'
851 | 127 | 127

1 1'
851 | 127 | 127

1 1'
865 | 127 | 127

1 1'
878 | 127 | 127

1 1'
891 | 127 | 127

1 1'
902 | 127 | 127

1 1'
902 | 127 | 127

1 1'
917 | 126 | 126

1 1'
929 | 124 | 124

1 1'
938 | 122 | 122

1 1'
955 | 120 | 120

1 1'
955 | 118 | 116

1 1'
968 | 114 | 114

1 1'
980 | 112 | 112

1 1'
990 | 110 | 110

1 1'
1005 | 108 | 108

1 1'
1005 | 106 | 104

1 1'
1019 | 102 | 102

1 1'
1033 | 100 | 100

1 1'
1047 | 98 | 98

1 1'
1059 | 94 | 94

1 1'
1059 | 92 | 92

1 1'
1072 | 90 | 90

1 1'
1086 | 88 | 86

1 1'
1097 | 84 | 84

1 1'
1110 | 82 | 82

1 1'
1110 | 80 | 80

1 1'
1123 | 78 | 78

1 1'
1137 | 76 | 76

1 1'
1149 | 74 | 72

1 1'
1160 | 70 | 70

1 1'
1160 | 68 | 68

1 1'
1175 | 66 | 66

1 1'
1188 | 64 | 64

1 1'
1197 | 62 | 62

1 1'
1211 | 60 | 58

1 1'
1211 | 56 | 56

1 1'
1225 | 54 | 54

1 1'
1237 | 52 | 52

1 1'
1251 | 50 | 48

1 1'
1261 | 48 | 46

1 1'
1261 | 44 | 44

1 1'
1273 | 44 | 42

1 1'
1288 | 40 | 40

1 1'
1300 | 38 | 38

1 1'
1311 | 36 | 36

1 1'

1311 | 34 | 34

1 1'
1323 | 32 | 32

1 1'
1333 | 30 | 30

1 1'
1349 | 28 | 26

1 1'
1361 | 26 | 24

1 1'
1361 | 22 | 22

1 1'
1373 | 20 | 20

1 1'
1383 | 18 | 18

1 1'
1398 | 16 | 16

1 1'
1410 | 14 | 14

1 1'
1410 | 12 | 12

1 1'
1423 | 10 | 10

1 1'
1435 | 8 | 8

1 1'
1448 | 6 | 6

1 1'
1467 | 6 | 6

1 1'
1467 | 4 | 4

1 1'
1488 | 2 | 2

1 1'
1508 | 0 | 0

1 1'
1528 | -2 | -2

1 1'
1554 | -4 | -6

1 1'
1554 | -6 | -6

1 1'
1579 | -8 | -8

1 1'
1605 | -8 | -8

1 1'
1630 | -6 | -6

1 1'
1630 | -6 | -6

1 1'
1664 | -4 | -4

1 1'
1692 | -2 | -2

1 1'
1720 | 0 | 0

1 1'
1750 | 0 | 0

1 1'
1750 | 2 | 2

1 1'
1782 | 2 | 2

1 1'
1813 | 0 | 0

1 1'
1844 | 0 | 0

1 1'
1875 | 0 | -2

1 1'
1875 | -2 | -2

1 1'
1910 | -2 | -2

1 1'
1945 | -2 | -2

1 1'
1970 | -2 | -2

1 1'
1995 | -4 | -4

1 1'
1995 | -4 | -4

1 1'
2021 | -2 | -2

1 1'
2048 | -2 | -2

1 1'
2076 | -2 | -2

1 1'
2098 | -2 | 0

1 1'
2098 | 0 | 0

1 1'
2123 | 0 | 0

1 1'
2143 | 0 | 0

1 1'
2163 | 0 | 0

1 1'
2181 | 0 | 0

1 1'
2181 | 0 | 0

1 1'
2203 | 0 | 0

1 1'
2223 | 127 | 127

2 1'
2239 | 127 | 127

2 1'

2259 | 127 | 127

2 1'
2259 | 127 | 127

2 1'
2278 | 127 | 127

2 1'
2295 | 127 | 127

2 1'
2311 | 127 | 127

2 1'
2325 | 127 | 127

2 1'
2325 | 127 | 127

2 1'
2344 | 127 | 127

2 1'
2359 | 127 | 127

2 1'
2372 | 127 | 127

2 1'
2386 | 127 | 127

2 1'
2386 | 127 | 127

2 1'
2402 | 127 | 127

2 1'
2416 | 127 | 127

2 1'
2429 | 127 | 127

2 1'
2442 | 127 | 127

2 1'
2442 | 127 | 127

2 1'
2455 | 127 | 127

2 1'
2472 | 127 | 127

2 1'
2486 | 127 | 127

2 1'
2498 | 127 | 126

2 1'
2498 | 124 | 124

2 1'
2512 | 122 | 122

2 1'
2525 | 120 | 120

2 1'
2538 | 118 | 118

2 1'
2550 | 116 | 116

2 1'
2550 | 114 | 112

2 1'
2565 | 112 | 110

2 1'
2577 | 108 | 108

2 1'
2590 | 106 | 106

2 1'
2601 | 104 | 104

2 1'
2601 | 102 | 102

2 1'
2614 | 100 | 98

2 1'
2623 | 96 | 96

2 1'
2638 | 94 | 94

2 1'
2653 | 92 | 92

2 1'
2653 | 90 | 88

2 1'
2668 | 86 | 86

2 1'
2679 | 84 | 84

2 1'
2690 | 82 | 80

2 1'
2705 | 78 | 78

2 1'
2705 | 76 | 76

2 1'
2718 | 74 | 72

2 1'
2732 | 70 | 70

2 1'
2747 | 68 | 68

2 1'
2760 | 64 | 64

2 1'
2760 | 62 | 62

2 1'
2772 | 60 | 60

2 1'
2784 | 58 | 56

2 1'
2798 | 56 | 54

2 1'
2812 | 52 | 52

2 1'
2812 | 50 | 50

2 1'
2824 | 48 | 48

2 1'

2835 | 46 | 46

2 1'
2848 | 44 | 44

2 1'
2860 | 42 | 42

2 1'
2860 | 40 | 38

2 1'
2871 | 38 | 36

2 1'
2884 | 34 | 34

2 1'
2896 | 32 | 32

2 1'
2907 | 30 | 30

2 1'
2907 | 28 | 28

2 1'
2921 | 26 | 24

2 1'
2936 | 22 | 22

2 1'
2947 | 20 | 20

2 1'
2961 | 18 | 18

2 1'
2961 | 16 | 16

2 1'
2972 | 14 | 14

2 1'
2982 | 12 | 12

2 1'
2997 | 10 | 10

2 1'
3010 | 8 | 8

2 1'
3010 | 6 | 6

2 1'
3029 | 6 | 6

2 1'
3051 | 4 | 4

2 1'
3074 | 2 | 0

2 1'
3095 | 0 | -2

2 1'
3095 | -4 | -4

2 1'
3119 | -6 | -6

2 1'
3145 | -8 | -8

2 1'
3172 | -8 | -8

2 1'
3200 | -8 | -8

2 1'
3200 | -6 | -6

2 1'
3230 | -6 | -4

2 1'
3259 | -4 | -2

2 1'
3288 | -2 | 0

2 1'
3318 | 0 | 0

2 1'
3318 | 2 | 2

2 1'
3353 | 2 | 2

2 1'
3381 | 2 | 2

2 1'
3413 | 2 | 2

2 1'
3413 | 2 | 2

2 1'
3449 | 0 | 0

2 1'
3481 | 0 | 0

2 1'
3510 | -2 | -2

2 1'
3537 | -2 | -2

2 1'
3537 | -4 | -4

2 1'
3565 | -4 | -4

2 1'
3590 | -4 | -4

2 1'
3615 | -4 | -4

2 1'
3638 | -4 | -4

2 1'
3638 | -2 | -2

2 1'
3665 | -2 | -2

2 1'
3687 | -2 | -2

2 1'
3706 | -2 | -2

2 1'
3728 | -2 | -2

2 1'
3728 | 0 | 0

2 1'

3745

0

0

2 1'
3764

0

0

2 1'
3788

0

0

2 1'
3801

0

0

2 1'
3801

0

0

2 1'
3819

0

0

2 1'
3837

0

0

2 1'
3852

0

0

2 1'
3867

0

0

2 1'
3867

0

0

2 1'
3881

0

0

2 1'
3899

0

0

2 1'
3914

0

0

2 1'
3926

0

0

2 1'
3926

0

0

2 1'
3939

0

0

2 1'
3953

0

0

2 1'
3968

0

0

2 1'
3981

0

0

2 1'
3981

0

0

2 1'
3995

0

0

2 1'
4005

0

0

2 1'
4020

0

0

2 1'
4032

0

0

2 1'
4032 | 127 | 127

3 1'
4045 | 127 | 127

3 1'
4058 | 127 | 127

3 1'
4072 | 127 | 127

3 1'
4083 | 127 | 127

3 1'
4083 | 127 | 127

3 1'
4096 | 127 | 127

3 1'
4107 | 127 | 127

3 1'
4120 | 127 | 127

3 1'
4132 | 127 | 127

3 1'
4132 | 127 | 127

3 1'
4143 | 127 | 127

3 1'
4159 | 127 | 127

3 1'
4170 | 127 | 127

3 1'
4179 | 127 | 127

3 1'
4179 | 127 | 127

3 1'
4192 | 127 | 127

3 1'
4206 | 127 | 127

3 1'
4218 | 127 | 127

3 1'
4229 | 127 | 127

3 1'
4229 | 127 | 127

3 1'
4243 | 127 | 127

3 1'
4254 | 127 | 127

3 1'
4268 | 127 | 127

3 1'
4278 | 127 | 127

3 1'
4278 | 127 | 126

3 1'
4290 | 124 | 124

3 1'
4301 | 124 | 124

3 1'
4307 | 124 | 124

3 1'

4313 | 124 | 124

3 1'
4313 | 124 | 124

3 1'
4315 | 124 | 124

3 1'
4323 | 124 | 124

3 1'
4331 | 126 | 126

3 1'
4335 | 126 | 126

3 1'
4335 | 126 | 126

3 1'
4341 | 127 | 127

3 1'
4347 | 127 | 127

3 1'
4356 | 127 | 127

3 1'
4366 | 127 | 127

3 1'
4366 | 127 | 127

3 1'
4372 | 127 | 127

3 1'
4380 | 127 | 127

3 1'
4389 | 127 | 127

3 1'
4399 | 127 | 127

3 1'
4399 | 127 | 127

3 1'
4406 | 127 | 127

3 1'
4413 | 127 | 127

3 1'
4425 | 127 | 127

3 1'
4435 | 127 | 127

3 1'
4435 | 127 | 127

3 1'
4446 | 127 | 127

3 1'
4454 | 127 | 127

3 1'
4462 | 127 | 127

3 1'
4472 | 127 | 127

3 1'
4472 | 127 | 127

3 1'
4482 | 127 | 127

3 1'
4496 | 127 | 127

3 1'
4506 | 127 | 127

3 1'
4514 | 127 | 127

3 1'
4514 | 127 | 127

3 1'
4525 | 127 | 127

3 1'
4536 | 127 | 127

3 1'
4546 | 127 | 127

3 1'
4555 | 127 | 127

3 1'
4555 | 127 | 127

3 1'
4569 | 127 | 127

3 1'
4584 | 127 | 127

3 1'
4598 | 127 | 127

3 1'
4610 | 127 | 127

3 1'
4610 | 127 | 127

3 1'
4622 | 127 | 127

3 1'
4635 | 127 | 127

3 1'
4647 | 127 | 127

3 1'
4657 | 127 | 127

3 1'
4657 | 127 | 127

3 1'
4669 | 127 | 127

3 1'
4681 | 127 | 127

3 1'
4692 | 127 | 127

3 1'
4708 | 127 | 127

3 1'
4708 | 127 | 127

3 1'
4724 | 127 | 127

3 1'

4735 | 127 | 127

3 1'
4749 | 127 | 127

3 1'
4761 | 127 | 127

3 1'
4761 | 127 | 127

3 1'
4776 | 127 | 127

3 1'
4789 | 127 | 127

3 1'
4802 | 127 | 127

3 1'
4812 | 127 | 127

3 1'
4812 | 127 | 127

3 1'
4824 | 127 | 127

3 1'
4837 | 127 | 127

3 1'
4857 | 127 | 127

3 1'
4857 | 127 | 127

3 1'
4882 | 127 | 127

3 1'
4894 | 127 | 127

3 1'
4908 | 127 | 127

3 1'
4922 | 127 | 127

3 1'
4934 | 127 | 127

3 1'
4946 | 127 | 127

3 1'
4959 | 127 | 127

3 1'
4959 | 127 | 127

3 1'
4969 | 127 | 127

3 1'
4978 | 126 | 126

3 1'
4990 | 126 | 126

3 1'
5004 | 126 | 126

3 1'
5004 | 124 | 124

3 1'
5016 | 124 | 124

3 1'
5030 | 124 | 124

3 1'
5043 | 124 | 124

3 1'
5053 | 124 | 124

3 1'
5053 | 124 | 124

3 1'
5066 | 122 | 122

3 1'
5077 | 122 | 122

3 1'
5088 | 122 | 122

3 1'
5100 | 122 | 122
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

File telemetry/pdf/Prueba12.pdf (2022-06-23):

Hoja1

Página

b'55 | 31 | 178 | 985
2 | 180 22.52
b'54 | 31 | 178 | 999
2 | 180 23.61
b'54 | 32 | 167 | 1009
2 | 180 24.87
b'53 | 33 | 178 | 1025
2 | 180 25.95
b'52 | 33 | 178 | 1035
2 | 180 27.15
b'52 | 178 | 166 | 1035
2 | 180 28.16
b'51 | 178 | 178 | 1047
2 | 180 29.29
b'50 | 178 | 24 | 1063
2 | 180 30.40
b'50 | 178 | 24 | 1075
2 | 180 31.60
b'49 | 178 | 178 | 1086
2 | 180 32.63
b'49 | 178 | 178 | 1086
2 | 180 33.61
b'49 | 178 | 24 | 1097
2 | 180 34.63
b'48 | 178 | 178 | 1109
2 | 180 35.78
b'178 | 178 | 178 | 1121
2 | 180 36.91
b'178 | 61 | 0 | 1137
2 | 180 37.90
b'178 | 61 | 0 | 1137
2 | 180 38.84
b'178 | 61 | 178 | 1147
2 | 180 39.87
b'178 | 62 | 13 | 1158
2 | 180 41.02
b'178 | 61 | 81 | 1170
2 | 180 42.10
b'178 | 61 | 81 | 1181
2 | 180 43.22
b'178 | 62 | 178 | 1181
2 | 180 44.29
b'178 | 62 | 12 | 1196
2 | 180 45.33
b'178 | 63 | 12 | 1206
2 | 180 46.46
b'178 | 63 | 178 | 1216
2 | 180 47.67
b'178 | 63 | 20 | 1231
2 | 180 48.86
b'178 | 63 | 56 | 1231
2 | 180 50.07
b'178 | 65 | 56 | 1241
2 | 180 51.28
b'178 | 66 | 71 | 1254
2 | 180 52.40
b'178 | 66 | 56 | 1268
2 | 180 53.58
b'178 | 66 | 57 | 1279
2 | 180 54.71
b'178 | 68 | 57 | 1279
2 | 180 55.87
b'178 | 68 | 57 | 1291
2 | 180 56.97
b'178 | 178 | 57 | 1304
2 | 180 58.14
b'178 | 178 | 55 | 1318
2 | 180 59.27
b'178 | 178 | 55 | 1330
2 | 180 60.50
b'178 | 178 | 55 | 1330
2 | 180 61.66
b'178 | 178 | 56 | 1341
2 | 180 62.90
b'178 | 178 | 56 | 1356
2 | 180 64.07
b'178 | 178 | 55 | 1368
2 | 180 65.43
b'178 | 178 | 55 | 1382
2 | 180 66.65
b'178 | 178 | 54 | 1382
2 | 180 67.93
b'178 | 41 | 54 | 1396
2 | 180 69.07
b'106 | 178 | 54 | 1409
2 | 180 70.24
b'106 | 178 | 54 | 1423
2 | 180 71.31
b'178 | 178 | 54 | 1432
2 | 180 72.27
b'178 | 178 | 54 | 1432
2 | 180 73.25
b'178 | 178 | 54 | 1443
2 | 180 74.23
b'178 | 81 | 55 | 1456
2 | 180 75.45
b'178 | 81 | 54 | 1467
2 | 180 76.62
b'178 | 178 | 54 | 1481
2 | 180 77.83
b'178 | 51 | 54 | 1481
2 | 180 78.97
b'112 | 51 | 53 | 1494
2 | 180 80.10
b'111 | 132 | 53 | 1505
2 | 180 81.22

b'111 | 132 | 53 | 1520
2 | 180 82.32
b'178 | 74 | 53 | 1530
2 | 180 83.33
b'178 | 74 | 52 | 1530
2 | 180 84.30
b'178 | 32 | 52 | 1542
2 | 180 85.16
b'178 | 31 | 52 | 1556
2 | 180 85.89
b'178 | 30 | 52 | 4
0 | 180 86.60
b'178 | 30 | 53 | 18
0 | 180 87.12
b'178 | 30 | 53 | 18
0 | 180 87.60
b'178 | 31 | 54 | 42
0 | 180 88.34
b'178 | 31 | 53 | 62
0 | 180 89.25
b'179 | 31 | 53 | 85
0 | 180 90.22
b'178 | 30 | 52 | 109
0 | 180 91.32
b'178 | 30 | 52 | 109
0 | 180 92.33
b'178 | 31 | 51 | 134
0 | 180 93.27
b'178 | 31 | 52 | 160
0 | 180 93.88
b'178 | 31 | 52 | 189
0 | 180 94.06
b'178 | 32 | 51 | 218
0 | 180 94.07
b'178 | 32 | 50 | 218
0 | 180 93.57
b'178 | 32 | 50 | 248
0 | 180 92.93
b'172 | 32 | 51 | 276
0 | 180 92.23
b'172 | 32 | 51 | 304
0 | 180 91.38
b'166 | 33 | 50 | 334
0 | 180 90.52
b'162 | 32 | 50 | 334
0 | 180 89.84
b'155 | 32 | 50 | 362
0 | 180 89.40
b'149 | 30 | 51 | 394
0 | 180 89.16
b'149 | 30 | 51 | 427
0 | 180 89.12
b'143 | 30 | 51 | 459
1 | 180 89.17
b'137 | 30 | 50 | 459
1 | 180 89.40
b'130 | 32 | 50 | 487
1 | 180 89.65
b'127 | 31 | 51 | 518
1 | 180 89.90
b'119 | 31 | 51 | 548
1 | 180 90.25
b'119 | 31 | 51 | 575
1 | 180 90.46
b'116 | 31 | 50 | 575
1 | 180 90.64
b'111 | 32 | 50 | 605
1 | 180 90.77
b'106 | 31 | 50 | 631
1 | 180 90.86
b'104 | 33 | 50 | 653
1 | 180 90.89
b'100 | 33 | 51 | 653
1 | 180 90.95
b'98 | 33 | 52 | 677
1 | 180 91.01
b'98 | 67 | 52 | 697
1 | 180 91.01
b'95 | 33 | 52 | 719
1 | 180 91.10
b'89 | 35 | 58 | 735
4 | 180 91.14
b'89 | 37 | 58 | 735
4 | 180 91.12
b'87 | 35 | 56 | 758
4 | 180 90.98
b'84 | 35 | 66 | 777
4 | 180 90.84
b'83 | 35 | 66 | 793
4 | 180 90.75
b'80 | 33 | 67 | 812
4 | 180 90.62
b'78 | 33 | 68 | 812
4 | 180 90.51
b'76 | 33 | 70 | 828
4 | 180 90.45
b'76 | 33 | 70 | 843
4 | 180 90.50
b'75 | 33 | 178 | 860
2 | 270 90.44
b'73 | 33 | 178 | 876
2 | 270 90.34
b'71 | 33 | 178 | 876
2 | 270 90.31
b'70 | 33 | 178 | 888
2 | 270 90.69

b'70 | 34 | 178 | 907
2 | 270 91.61
b'68 | 34 | 178 | 922
2 | 270 92.90
b'68 | 34 | 178 | 933
2 | 270 94.25
b'66 | 35 | 178 | 933
2 | 270 95.50
b'64 | 36 | 178 | 947
2 | 270 96.78
b'64 | 39 | 178 | 961
2 | 270 98.08
b'61 | 39 | 178 | 975
2 | 270 99.45
b'61 | 38 | 178 | 989
2 | 270 100.77
b'59 | 38 | 178 | 989
2 | 270 101.95
b'58 | 38 | 178 | 1002
2 | 270 103.31
b'57 | 40 | 178 | 1018
2 | 270 104.52
b'56 | 40 | 178 | 1028
2 | 270 105.65
b'56 | 41 | 178 | 1041
2 | 270 106.70
b'55 | 41 | 178 | 1041
2 | 270 107.93
b'55 | 43 | 178 | 1054
2 | 270 109.04
b'55 | 43 | 178 | 1067
2 | 270 110.33
b'53 | 178 | 178 | 1079
2 | 270 111.51
b'51 | 178 | 178 | 1095
2 | 270 112.85
b'51 | 178 | 178 | 1095
2 | 270 114.08
b'50 | 178 | 178 | 1105
2 | 270 115.30
b'50 | 142 | 178 | 1116
2 | 270 116.32
b'48 | 141 | 84 | 1130
2 | 270 117.41
b'48 | 141 | 178 | 1142
2 | 270 118.58
b'48 | 119 | 178 | 1142
2 | 270 119.80
b'47 | 125 | 80 | 1157
2 | 270 121.03
b'46 | 125 | 80 | 1167
2 | 270 122.26
b'46 | 140 | 178 | 1181
2 | 270 123.46
b'44 | 140 | 68 | 1194
2 | 270 124.65
b'44 | 125 | 178 | 1194
2 | 270 125.87
b'43 | 125 | 84 | 1208
2 | 270 127.19
b'43 | 126 | 84 | 1219
2 | 270 128.43
b'42 | 126 | 79 | 1234
2 | 270 129.65
b'178 | 126 | 79 | 1246
2 | 270 130.88
b'114 | 143 | 80 | 1246
2 | 270 131.94
b'114 | 143 | 178 | 1260
2 | 270 133.11
b'178 | 143 | 178 | 1274
2 | 270 134.29
b'178 | 145 | 0 | 1283
2 | 270 135.38
b'178 | 145 | 0 | 1297
2 | 270 136.50
b'102 | 144 | 71 | 1297
2 | 270 137.54
b'102 | 145 | 71 | 1310
2 | 270 138.48
b'110 | 145 | 70 | 1322
2 | 270 139.42
b'110 | 147 | 70 | 1338
2 | 270 140.49
b'105 | 148 | 72 | 1349
2 | 270 141.46
b'178 | 148 | 72 | 1349
2 | 270 142.71
b'178 | 147 | 178 | 1359
2 | 270 143.82
b'178 | 147 | 0 | 1372
2 | 270 144.91
b'178 | 149 | 0 | 1383
2 | 270 145.92
b'178 | 151 | 69 | 1397
2 | 270 147.05
b'178 | 151 | 69 | 1397
2 | 270 148.05
b'178 | 178 | 67 | 1409
2 | 270 149.20
b'178 | 178 | 76 | 1421
2 | 270 150.31
b'178 | 178 | 76 | 1434
2 | 270 151.48
b'178 | 178 | 72 | 1445
2 | 270 152.67

b'178 | 178 | 72 | 1445
2 | 270 153.79
b'178 | 178 | 65 | 1454
2 | 270 154.75
b'178 | 178 | 65 | 1470
2 | 270 155.72
b'178 | 178 | 67 | 1483
2 | 270 156.80
b'178 | 178 | 65 | 1495
2 | 270 157.83
b'178 | 178 | 75 | 1495
2 | 270 159.01
b'178 | 178 | 75 | 1509
2 | 270 160.15
b'178 | 178 | 64 | 1519
2 | 270 161.31
b'178 | 28 | 64 | 1532
2 | 270 162.47
b'178 | 178 | 63 | 1548
2 | 270 163.72
b'178 | 178 | 63 | 1548
2 | 270 164.97
b'178 | 178 | 63 | 1558
2 | 270 166.18
b'178 | 178 | 61 | 1570
2 | 270 167.34
b'178 | 178 | 61 | 1584
2 | 270 168.46
b'178 | 35 | 61 | 1595
2 | 270 169.61
b'178 | 26 | 61 | 1595
2 | 270 170.70
b'178 | 26 | 61 | 1606
2 | 270 171.91
b'178 | 26 | 61 | 1621
2 | 270 173.04
b'178 | 27 | 61 | 1633
2 | 270 174.01
b'178 | 26 | 60 | 1644
2 | 270 174.96
b'178 | 27 | 60 | 1644
2 | 270 175.84
b'179 | 27 | 62 | -2
0 | 270 176.58
b'178 | 27 | 62 | 13
0 | 270 177.26
b'178 | 27 | 60 | 39
0 | 270 178.04
b'178 | 27 | 63 | 60
0 | 270 179.16
b'178 | 27 | 63 | 60
0 | 270 180.40
b'178 | 28 | 57 | 85
0 | 270 181.82
b'178 | 28 | 57 | 108
0 | 270 182.95
b'178 | 28 | 57 | 132
0 | 270 183.78
b'175 | 29 | 57 | 158
0 | 270 184.22
b'175 | 29 | 57 | 158
0 | 270 184.06
b'170 | 29 | 56 | 185
0 | 270 183.62
b'166 | 29 | 56 | 211
0 | 270 182.75
b'161 | 29 | 56 | 240
0 | 270 181.81
b'156 | 28 | 56 | 240
0 | 270 180.79
b'156 | 28 | 56 | 271
0 | 270 180.02
b'152 | 28 | 57 | 303
0 | 270 179.50
b'147 | 29 | 57 | 332
0 | 270 179.24
b'140 | 31 | 57 | 360
0 | 270 179.14
b'135 | 27 | 57 | 360
0 | 270 179.21
b'128 | 27 | 57 | 392
0 | 270 179.39
b'128 | 27 | 57 | 425
0 | 270 179.64
b'124 | 26 | 57 | 459
1 | 270 179.84
b'118 | 26 | 57 | 489
1 | 270 180.17
b'111 | 26 | 57 | 489
1 | 270 180.60
b'106 | 26 | 57 | 514
1 | 270 180.91
b'100 | 26 | 57 | 543
1 | 270 181.14
b'96 | 26 | 57 | 570
1 | 270 181.26
b'96 | 26 | 56 | 596
1 | 270 181.28
b'92 | 27 | 56 | 596
1 | 270 181.27
b'84 | 28 | 56 | 620
4 | 270 181.11
b'84 | 27 | 56 | 649
4 | 270 180.86
b'81 | 27 | 56 | 667
4 | 270 180.68

b'78 | 27 | 56 | 684
4 | 270 180.59
b'75 | 26 | 57 | 684
4 | 270 180.50
b'74 | 26 | 57 | 704
4 | 270 180.46
b'71 | 27 | 56 | 720
4 | 270 180.44
b'70 | 26 | 56 | 737
4 | 270 180.50
b'70 | 26 | 56 | 756
4 | 270 180.43
b'65 | 26 | 56 | 756
4 | 270 180.34
b'65 | 26 | 56 | 776
4 | 270 180.24
b'62 | 26 | 57 | 796
4 | 270 180.22
b'58 | 25 | 58 | 814
4 | 270 180.20
b'57 | 25 | 58 | 829
4 | 270 180.16
b'55 | 25 | 58 | 829
4 | 270 180.13
b'55 | 25 | 58 | 843
4 | 270 180.11
b'54 | 25 | 59 | 858
4 | 270 180.06
b'52 | 25 | 59 | 875
4 | 270 180.01
b'49 | 25 | 59 | 889
4 | 270 179.99
b'48 | 25 | 60 | 889
4 | 270 179.98
b'47 | 25 | 60 | 903
4 | 270 179.98
b'47 | 26 | 59 | 915
4 | 270 179.95
b'46 | 26 | 61 | 930
4 | 270 179.92
b'44 | 26 | 61 | 944
4 | 270 179.86
b'44 | 26 | 61 | 944
4 | 270 179.87
b'41 | 25 | 63 | 957
4 | 270 179.95
b'40 | 25 | 63 | 970
4 | 270 180.00
b'40 | 25 | 178 | 986
2 | 360 180.03
b'38 | 25 | 178 | 998
2 | 360 180.15
b'37 | 25 | 178 | 998
2 | 360 180.24
b'37 | 25 | 78 | 1011
2 | 360 180.66
b'34 | 25 | 78 | 1024
2 | 360 181.57
b'34 | 26 | 78 | 1038
2 | 360 182.82
b'32 | 26 | 78 | 1050
2 | 360 184.10
b'32 | 26 | 78 | 1050
2 | 360 185.19
b'32 | 27 | 78 | 1062
2 | 360 186.29
b'30 | 27 | 178 | 1076
2 | 360 187.56
b'28 | 27 | 178 | 1088
2 | 360 188.70
b'28 | 29 | 78 | 1100
2 | 360 189.81
b'27 | 28 | 79 | 1100
2 | 360 190.96
b'26 | 29 | 78 | 1114
2 | 360 192.09
b'26 | 30 | 77 | 1126
2 | 360 193.26
b'24 | 30 | 77 | 1138
2 | 360 194.36
b'24 | 32 | 77 | 1150
2 | 360 195.54
b'23 | 32 | 78 | 1150
2 | 360 196.80
b'22 | 32 | 77 | 1161
2 | 360 198.02
b'25 | 32 | 178 | 1174
2 | 360 199.21
b'23 | 122 | 66 | 1183
2 | 360 200.39
b'19 | 36 | 65 | 1196
2 | 360 201.52
b'18 | 36 | 64 | 1196
2 | 360 202.76
b'17 | 36 | 65 | 1207
2 | 360 204.01
b'17 | 38 | 65 | 1221
2 | 360 205.29
b'17 | 39 | 63 | 1234
2 | 360 206.57
b'16 | 40 | 64 | 1247
2 | 360 207.90
b'16 | 40 | 63 | 1247
2 | 360 209.05
b'16 | 42 | 63 | 1258
2 | 360 210.28

b'178 | 42 | 63 | 1274
2 | 360 211.42
b'178 | 167 | 63 | 1284
2 | 360 212.67
b'178 | 48 | 63 | 1296
2 | 360 213.88
b'178 | 163 | 63 | 1296
2 | 360 215.17
b'178 | 163 | 63 | 1309
2 | 360 216.14
b'178 | 178 | 63 | 1321
2 | 360 217.20
b'178 | 178 | 62 | 1335
2 | 360 218.28
b'178 | 178 | 62 | 1347
2 | 360 219.45
b'178 | 178 | 62 | 1347
2 | 360 220.49
b'178 | 178 | 62 | 1358
2 | 360 221.53
b'178 | 178 | 62 | 1369
2 | 360 222.16
b'178 | 178 | 62 | 1379
2 | 360 222.40
b'178 | 170 | 62 | 1385
2 | 360 222.10
b'178 | 170 | 62 | 1385
2 | 360 221.51
b'178 | 172 | 62 | 1389
2 | 360 221.14
b'178 | 178 | 62 | 1389
2 | 360 221.06
b'178 | 178 | 62 | 1397
2 | 360 221.07
b'178 | 178 | 62 | 1405
2 | 360 221.08
b'178 | 178 | 61 | 1405
2 | 360 221.04
b'178 | 178 | 61 | 1413
2 | 360 220.86
b'178 | 178 | 62 | 1416
2 | 360 220.55
b'178 | 178 | 61 | 1418
2 | 360 220.31
b'178 | 178 | 61 | 1420
2 | 360 220.16
b'178 | 178 | 61 | 1420
2 | 360 220.04
b'178 | 178 | 61 | 1428
2 | 360 219.87
b'178 | 178 | 61 | 1439
2 | 360 219.44
b'178 | 178 | 61 | 1445
2 | 360 218.82
b'178 | 178 | 61 | 1449
2 | 360 218.30
b'178 | 178 | 61 | 1449
2 | 360 218.05
b'178 | 178 | 61 | 1453
2 | 360 217.82
b'178 | 178 | 62 | 1463
2 | 360 217.40
b'178 | 178 | 62 | 1475
2 | 360 216.77
b'178 | 178 | 62 | 1485
2 | 360 216.07
b'178 | 178 | 62 | 1485
2 | 360 215.44
b'7 | 178 | 62 | 1488
2 | 360 215.10
b'7 | 178 | 62 | 1492
2 | 360 214.79
b'7 | 142 | 60 | 1503
2 | 360 214.40
b'7 | 144 | 64 | 1515
2 | 360 213.82
b'7 | 144 | 64 | 1515
2 | 360 213.19
b'7 | 144 | 63 | 1519
2 | 360 212.74
b'6 | 144 | 63 | 1523
2 | 360 212.41
b'6 | 142 | 178 | 1535
2 | 360 211.98
b'5 | 143 | 3 | 1547
2 | 360 211.43
b'5 | 173 | 178 | 1547
2 | 360 210.76
b'6 | 142 | 2 | 1562
2 | 360 209.96
b'5 | 142 | 71 | 1570
2 | 360 209.32
b'6 | 142 | 71 | 1578
2 | 360 208.64
b'6 | 143 | 178 | 1590
2 | 360 207.95
b'6 | 143 | 2 | 1590
2 | 360 207.17
b'5 | 144 | 178 | 1599
2 | 360 206.43
b'4 | 142 | 3 | 1609
2 | 360 205.68
b'4 | 142 | 3 | 1617
2 | 360 205.03
b'4 | 142 | 178 | 1624
2 | 360 204.38

b'4 | 143 | 3 | 1624
2 | 360 203.71
b'5 | 143 | 3 | 1635
2 | 360 202.88
b'5 | 114 | 2 | 1648
2 | 360 202.06
b'4 | 114 | 178 | 1660
2 | 360 201.15
b'4 | 144 | 178 | 1671
2 | 360 200.25
b'4 | 108 | 179 | 1671
2 | 360 199.53
b'4 | 108 | 179 | 1680
2 | 360 198.97
b'5 | 145 | 178 | 1688
2 | 360 198.40
b'5 | 114 | 178 | 1700
2 | 360 197.87
b'4 | 114 | 178 | 1712
2 | 360 197.24
b'4 | 148 | 178 | 1712
2 | 360 196.59
b'4 | 115 | 178 | 1724
2 | 360 195.90
b'4 | 115 | 178 | 1738
2 | 360 195.24
b'3 | 147 | 73 | 1751
2 | 360 194.49
b'3 | 147 | 63 | 1763
2 | 360 193.69
b'4 | 110 | 63 | 1763
2 | 360 192.99
b'4 | 110 | 56 | 1772
2 | 360 192.33
b'5 | 58 | 78 | 1780
2 | 360 191.71
b'8 | 57 | 178 | 1790
2 | 360 191.14
b'8 | 56 | 78 | 1798
2 | 360 190.61
b'7 | 56 | 77 | 1798
2 | 360 189.95
b'4 | 56 | 178 | 1814
2 | 360 189.28
b'4 | 56 | 178 | 1829
2 | 360 188.52
b'4 | 57 | 78 | 1837
2 | 360 187.76
b'6 | 56 | 66 | 1847
2 | 360 187.21
b'6 | 57 | 64 | 1847
2 | 360 186.72
b'6 | 57 | 77 | 1852
2 | 360 186.37
b'6 | 58 | 77 | 1862
2 | 360 186.01
b'6 | 56 | 64 | 1876
2 | 360 185.70
b'6 | 57 | 77 | 1890
2 | 360 185.31
b'7 | 57 | 77 | 1890
2 | 360 184.97
b'7 | 57 | 76 | 1906
2 | 360 184.67
b'6 | 56 | 76 | 1917
2 | 360 184.36
b'6 | 56 | 76 | 1930
2 | 360 184.15
b'6 | 57 | 77 | 1941
2 | 360 183.99
b'6 | 56 | 178 | 1941
2 | 360 183.87

985 | 127 | 127

1 1'
999 | 127 | 127

1 1'
1009 | 127 | 127

1 1'
1025 | 127 | 127

1 1'
1035 | 127 | 126

1 1'
1035 | 126 | 124

1 1'
1047 | 122 | 122

1 1'
1063 | 120 | 120

1 1'
1075 | 118 | 118

1 1'
1086 | 116 | 116

1 1'
1086 | 114 | 114

1 1'
1097 | 112 | 112

1 1'
1109 | 110 | 110

1 1'
1121 | 108 | 108

1 1'
1137 | 106 | 106

1 1'
1137 | 104 | 104

1 1'
1147 | 102 | 102

1 1'
1158 | 100 | 98

1 1'
1170 | 98 | 96

1 1'
1181 | 94 | 94

1 1'
1181 | 92 | 92

1 1'
1196 | 90 | 90

1 1'
1206 | 88 | 88

1 1'
1216 | 86 | 86

1 1'
1231 | 84 | 84

1 1'
1231 | 82 | 80

1 1'
1241 | 78 | 78

1 1'
1254 | 76 | 76

1 1'
1268 | 74 | 74

1 1'
1279 | 72 | 72

1 1'
1279 | 70 | 70

1 1'
1291 | 68 | 68

1 1'
1304 | 66 | 64

1 1'
1318 | 62 | 62

1 1'
1330 | 60 | 60

1 1'
1330 | 58 | 58

1 1'
1341 | 56 | 56

1 1'
1356 | 54 | 52

1 1'
1368 | 50 | 50

1 1'
1382 | 48 | 48

1 1'
1382 | 46 | 46

1 1'
1396 | 44 | 42

1 1'
1409 | 42 | 40

1 1'
1423 | 38 | 38

1 1'
1432 | 36 | 36

1 1'
1432 | 34 | 34

1 1'
1443 | 32 | 32

1 1'
1456 | 30 | 30

1 1'
1467 | 28 | 28

1 1'
1481 | 26 | 26

1 1'
1481 | 24 | 24

1 1'
1494 | 22 | 20

1 1'
1505 | 18 | 18

1 1'

1520 | 16 | 16

1 1'
1530 | 14 | 14

1 1'
1530 | 12 | 12

1 1'
1542 | 10 | 10

1 1'
1556 | 10 | 10

1 1'
1568 | 8 | 8

1 1'
1582 | 6 | 6

1 1'
1582 | 6 | 6

1 1'
1606 | 4 | 4

1 1'
1626 | 2 | 2

1 1'
1649 | 0 | 0

1 1'
1673 | -2 | -2

1 1'
1673 | -4 | -4

1 1'
1698 | -6 | -6

1 1'
1724 | -6 | -6

1 1'
1753 | -8 | -8

1 1'
1782 | -8 | -8

1 1'
1782 | -6 | -6

1 1'
1812 | -6 | -4

1 1'
1840 | -4 | -4

1 1'
1868 | -2 | -2

1 1'
1898 | 0 | 0

1 1'
1898 | 2 | 2

1 1'
1926 | 2 | 2

1 1'
1958 | 2 | 2

1 1'
1991 | 2 | 2

1 1'
2023 | 2 | 2

1 1'
2023 | 2 | 2

1 1'
2051 | 2 | 2

1 1'
2082 | 2 | 2

1 1'
2112 | 0 | 0

1 1'
2139 | 0 | 0

1 1'
2139 | 0 | 0

1 1'
2169 | 0 | 0

1 1'
2195 | 0 | 0

1 1'
2217 | 0 | 0

1 1'
2217 | 0 | 0

1 1'
2241 | -2 | -2

1 1'
2261 | -2 | -2

1 1'
2283 | -2 | -2

1 1'
2299 | -2 | -2

1 1'
2299 | -2 | -2

1 1'
2322 | -2 | 0

1 1'
2341 | 0 | 0

1 1'
2357 | 0 | 0

1 1'
2376 | 0 | 0
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

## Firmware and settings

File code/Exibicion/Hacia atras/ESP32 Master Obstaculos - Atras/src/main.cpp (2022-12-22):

#include <Arduino.h>
#include <Wire.h>
#include <MPU9250.h>
#include <WebServer.h>
#include <WiFi.h>
#include <WiFiUdp.h>
#include <Pixy2.h>
#include <ESP32Servo.h>

#define tamanoMinimodeEsquive 35  //55
#define GreenSignature 1
#define RedSignature 2

#define EncodersPorCM 14

#define PIN_BOTON 13
#define PIN_BOCINA 14 //Altavoz para depuracion ********************************************************************************
#define OffsetMuroInterior 5
#define OffsetMuroExterior 5

#define PIN_SERVO_CAM 33      // Servo de la camara

#define servoKP 1.5
#define servoKD 0
int _setAngleAnterior;    // Valor del _setAngle anterior

#define posicionKP 0.4
#define posicionKD 20
int posicionObjetivo = 0;
int ErrorPosicionActual = 0;
int ErrorPosicionAnterior = 0;

float valorBrujula = 0;   // + anti-clockwise | - clockwise
float offset;
int giros = 0;
bool sentidoGiro = true;      // True -> Izquierda   |   False -> Derecha
int sentidoParaCorregirPosicion = 1;   //1 si izquierda | -1 si derecha
bool LecturaGiro = true;

int ErrorDireccionAnterior = 0;
int ErrorDireccionActual = 0;
int direccionObjetivo = 0;

uint32_t Duracion_de_la_muestra = 0;

MPU9250 mpu;
Pixy2 pixy;
Servo servo;

byte medidasUltrasonidos[4];
byte ultraFrontal = 0;
byte ultraDerecho = 1;
byte ultraIzquierdo = 2;
byte ultraTrasero = 3;

byte medidasLaseres[3];

long medidaencoder = 0;
long prev_medidaencoder = 0;
long MarcaEncoder = 0;

bool forward = true;

double posicionX = 0;   // 0 en el centro  | + izquierda | - derecha
double posicionY = 0;   // 0 pared trasera | + forward   | - backwards
bool corregirX = false; // Al inicio no se corrige

enum e{
  Inicio,
  Recto,
  DecidiendoGiro,
  Final
};

byte estado;


/*void Calibrar(){ // función para calibrar ( revisar )
  mpu.verbose(true);  
  delay(1000);
  mpu.calibrateMag();
  mpu.calibrateAccelGyro();
  mpu.verbose(false);
  saveCalibration();
}*/

// Devuelve la posición donde hay que poner el servo
int ErrorDireccion(int bearing, int target) {
  int error = target - bearing;
  return error;
}

// I2C Arduino Nano Slave 1

long medirEncoder() {
  Wire.beginTransmission(4);
  Wire.write(1);
  Wire.endTransmission();
  Wire.requestFrom(4,4);
  long _medidaEncoder;
  byte iteracion = 0;
  while( iteracion < 4){
    _medidaEncoder = _medidaEncoder | Wire.read()<<(8*iteracion);
    iteracion++;
  }
  return _medidaEncoder;
}

void medirUltrasonidos() {
  Wire.beginTransmission(4);
  Wire.write(2);
  Wire.endTransmission();
  Wire.requestFrom(4,4);
  byte iteracion = 0;
  while (Wire.available()) {
    medidasUltrasonidos[iteracion] = Wire.read();
    iteracion ++;
  }
}

void medirLaseres();
void distanceTelemetria();

void MantenimientoSensores(){
  while(true){
    Wire.beginTransmission(4);
    Wire.write(6);
    Wire.endTransmission();
    Wire.requestFrom(4,4);
    byte iteracion = 0;
    while (Wire.available()) {
      medidasUltrasonidos[iteracion] = Wire.read();
      iteracion ++;
    }
    medirLaseres();
    distanceTelemetria();
    delay(100);
  }
}

void setVelocidad(int velocidad){
  Wire.beginTransmission(4);
  Wire.write(3);
  if(velocidad<0){
    Wire.write(-velocidad);
    Wire.write(0);
    forward = false;
  }else{
    Wire.write(velocidad);
    Wire.write(2);
    forward = true;
  }
  Wire.endTransmission();
}

void setGiro(int posicionServo){
  Wire.beginTransmission(4);
  Wire.write(4);
  if(posicionServo<0){
    Wire.write(-posicionServo);
    Wire.write(0);
  }else{
    Wire.write(posicionServo);
    Wire.write(1);
  }
  Wire.endTransmission();
}

void setEnable(int motrorEnable){
  Wire.beginTransmission(4);
  Wire.write(5);
  Wire.write(motrorEnable);
  Wire.endTransmission();
}

// I2C Arduino Nano Every Slave 2

void medirLaseres() {
  Wire.beginTransmission(5);
  Wire.write(1);
  Wire.endTransmission();
  Wire.requestFrom(5,3);
  byte iteracion = 0;
  while (Wire.available()) {
    medidasLaseres[iteracion] = Wire.read();
    iteracion ++;
  }
}

// Telemetria

void enviarMensaje(int numero) {
 Serial.println(numero);
}
void enviarMensaje(String texto) {
 Serial.println(texto);
}

void posicionTelemetria() {
  Serial.print("\t");
  Serial.print(valorBrujula);
  Serial.print(",");
  Serial.print("\t");
  Serial.print(posicionObjetivo);
  Serial.print(",");
  Serial.print("\t");
  Serial.print(direccionObjetivo);
  Serial.print(",");
  Serial.print("\t");
  Serial.print(posicionX);
  Serial.print(",");
  Serial.print("\t");
  Serial.println(posicionY);
}
/*
void distanceTelemetria() {
Serial.print("\t");
Serial.print(medidasUltrasonidos[ultraFrontal]);
Serial.print("\t");
Serial.print(medidasUltrasonidos[ultraDerecho]);
Serial.print("\t");
Serial.print(medidasUltrasonidos[ultraIzquierdo]);
Serial.print("\t");
Serial.print(medidasUltrasonidos[ultraTrasero]);
Serial.print("\t");
Serial.print(medidasLaseres[ultraFrontal]);
Serial.print("\t");
Serial.print(medidasLaseres[ultraDerecho]);
Serial.print("\t");
Serial.println(medidasLaseres[ultraIzquierdo]);
}

void EnviarTelemetria()
{
  Serial.print("\t");
  Serial.print(estado);
  Serial.print(",");
  Serial.print("\t");
  Serial.print(medidasUltrasonidos[ultraFrontal]);
  Serial.print(",");
  Serial.print("\t");
  Serial.print(medidasUltrasonidos[ultraTrasero]);
  Serial.print(",");
  Serial.print("\t");
  Serial.print(medidasUltrasonidos[ultraDerecho]);
  Serial.print(",");
  Serial.print("\t");
  Serial.print(medidasUltrasonidos[ultraIzquierdo]);
  Serial.print(",");
  Serial.print("\t");
  Serial.print(MarcaEncoder);
  Serial.print(",");
  Serial.print("\t");
  Serial.print(medidaencoder);
  Serial.print(",");
  Serial.print("\t");
  Serial.print(medidaencoder - MarcaEncoder);
  Serial.print(",");
  Serial.print("\t");
  Serial.print(sentidoGiro);
  Serial.print(",");
  Serial.print("\t");
  Serial.print(direccionObjetivo);
  Serial.print(",");
  Serial.print("\t");
  Serial.print(_setAngleAnterior);
  Serial.print(",");
  Serial.print("\t");
  Serial.print(valorBrujula);
  Serial.print(",");
  Serial.print("\t");
  Serial.print(posicionX);
  Serial.print(",");
  Serial.print("\t");
  Serial.print(posicionY);
  Serial.print("\t");
  Serial.println(ErrorDireccionActual);
}*/

// Obtencion de la posicion

void posicionInicial() {
  medirUltrasonidos();
  /* if ((medidasUltrasonidos[ultraTrasero] > 90) && (medidasUltrasonidos[ultraTrasero] < 140)){
    posicionY = 105 * EncodersPorCM;
  } else if ((medidasUltrasonidos[ultraFrontal] > 90) && (medidasUltrasonidos[ultraFrontal] < 140)){
    posicionY = 160 * EncodersPorCM;
  } */
  posicionY = 105 * EncodersPorCM; //aaaaaatenccccciiiiooon, borar cuando el sensor funcione
  //EnviarTelemetria();
}

void resetPosicion(bool corregir) { // Corregir True -> Con ultrasonidos      Corregir False -> Con operaciones
  if (corregir) {   //No se usa esta parte, siempre el else hasta una posible mejora en la version 2.1
    if (sentidoGiro) {
      posicionX = (50 - medidasUltrasonidos[ultraDerecho]) * EncodersPorCM;
    } else {
      posicionX = (50 - medidasUltrasonidos[ultraIzquierdo]) * EncodersPorCM;
    }
    posicionY = medidasUltrasonidos[ultraTrasero] * EncodersPorCM;
  } else {
    double _posX = posicionX;
    posicionX = 250 * EncodersPorCM - posicionY - 10 * EncodersPorCM;
    if (sentidoGiro) {
      posicionY = _posX + 50 * EncodersPorCM;
    } else {
      posicionX = -posicionX;
      posicionY = -_posX + 50 * EncodersPorCM;
    }
    posicionObjetivo = 0;
  }
}

void checkGiro() {
  if (sentidoGiro) {
    if ((posicionY >= 160 * EncodersPorCM) && (posicionX >= 0)) {
      resetPosicion(false);
      giros ++;
      corregirX = true;
    } else if ((posicionY >= 195 * EncodersPorCM) && (posicionX <= 0)) {
      resetPosicion(false);
      giros ++;
      corregirX = true;
    }
  } else {
    if ((posicionY >= 170 * EncodersPorCM) && (posicionX <= 0)) {
      resetPosicion(false);
      giros --;
      corregirX = true;
    } else if ((posicionY >= 195 * EncodersPorCM) && (posicionX >= 0)) {
      resetPosicion(false);
      giros --;
      corregirX = true;
    }
  }
}

void corregirPosicion() {
  if (posicionY <= 100) {
    if (abs(abs(valorBrujula) - 90 * (abs(giros)-1)) <= 10) {   //Parece que funciona, soy Pedro
  //if (abs(valorBrujula - 90 * sentidoParaCorregirPosicion * (giros-1) <= 10) { //************************************************************************1->10
      digitalWrite(PIN_BOCINA,HIGH);
      if ((posicionX <= 140) && (sentidoGiro)) {
        posicionX = (medidasLaseres[ultraFrontal] - 50 - OffsetMuroExterior + 20) * EncodersPorCM;  //20 porque cuando corrige hay que restar la distancia entre el sensor y el centro del eje trasero
        //posicionX = medidasLaseres[ultraFrontal] * EncodersPorCM - 50 * EncodersPorCM - OffsetMuroExterior * EncodersPorCM + 20 * EncodersPorCM;
        //posicionY = medidasLaseres[ultraDerecho] * EncodersPorCM + 3 * EncodersPorCM;
      } else if ((posicionX >= -140) && (!sentidoGiro)) {
        posicionX = (50 + OffsetMuroExterior - medidasLaseres[ultraFrontal] - 20) * EncodersPorCM;
        //posicionX = 50 * EncodersPorCM + OffsetMuroExterior * EncodersPorCM - medidasLaseres[ultraFrontal] * EncodersPorCM - 20 * EncodersPorCM;
        //posicionY = medidasLaseres[ultraIzquierdo] * EncodersPorCM + 3 * EncodersPorCM;
      }
    }else{
      digitalWrite(PIN_BOCINA,LOW);
    }
  }
}

void posicionamiento() {
  ErrorPosicionAnterior = ErrorPosicionActual;
  ErrorPosicionActual = ErrorDireccion(posicionX, posicionObjetivo);
  if (posicionY <= 100 * EncodersPorCM) {
    direccionObjetivo = constrain(posicionKP * ErrorPosicionActual + posicionKD * (ErrorPosicionActual - ErrorPosicionAnterior), -100, 100);
  } else {
    direccionObjetivo = constrain(posicionKP * ErrorPosicionActual + posicionKD * (ErrorPosicionActual - ErrorPosicionAnterior), -85, 85);
  }
}

// Camara

// angulo € [-90, 90]
void moverCamara(int angulo) {  // 0 == 85 | min == 0 | max == 170
  int _ang = map(angulo*1.2 + 90, 0, 180, 0, 170);  //********************************************************Aumentar o siminuir
  servo.write(constrain(_ang, 50, 130));
}

// Mover el automaticamente el servo de la camara
void autoMoverCamara(double _posXblock) {
  double posicionBloqueX = 0;
  double posicionBloqueY = 0;
  int _ang;
  if (posicionY <= 95 * EncodersPorCM){
    posicionBloqueY = 90 * EncodersPorCM;
  } else if (posicionY <= 125 * EncodersPorCM) {
    posicionBloqueY = 140 * EncodersPorCM;
  } else if (posicionY <= 150 * EncodersPorCM) {
    posicionBloqueY = 190 * EncodersPorCM;
  }
  //_ang = 180 / M_PI * atan2(posicionBloqueX - posicionX, posicionBloqueY - posicionY);
  //int _offsetLapAngle = 90 * giros;
  //moverCamara(_ang - valorBrujula + _offsetLapAngle);
  if (posicionBloqueY) {
    _ang = 180 / M_PI * atan2(posicionBloqueX - posicionX, posicionBloqueY - posicionY);
    int _offsetLapAngle = 90 * giros;
    moverCamara(_ang - valorBrujula + _offsetLapAngle);
  } else {
    if (sentidoGiro) {
      moverCamara(45);
    } else {
      moverCamara(-45);
    }
  }
}

// Comienzo del programa

void setup() {
  delay(500);

  pixy.init();
  
  ESP32PWM::allocateTimer(0); // Iniciar timers del PWM
	ESP32PWM::allocateTimer(1);
	ESP32PWM::allocateTimer(2);
	ESP32PWM::allocateTimer(3);
	servo.setPeriodHertz(50);
  servo.attach(PIN_SERVO_CAM);
  moverCamara(0);

  Serial.begin(115200);

  pinMode(PIN_BOTON ,INPUT_PULLUP);
  pinMode(LED_BUILTIN,OUTPUT);
  pinMode(PIN_BOCINA,OUTPUT);

  Wire.begin();
  uint32_t freq = 400000;
  Wire1.begin(15,4,freq);
  delay(100);

  //MantenimientoSensores();

  estado = e::Inicio;

  WiFi.disconnect(true);
  WiFi.mode(WIFI_OFF);
  //Calibrar();

  for(int i = 0; i<20 ; i++){
    digitalWrite(LED_BUILTIN, !digitalRead(LED_BUILTIN));
    delay(100);
  }
  MPU9250Setting setting;
    setting.accel_fs_sel = ACCEL_FS_SEL::A16G;
    setting.gyro_fs_sel = GYRO_FS_SEL::G2000DPS;
    setting.mag_output_bits = MAG_OUTPUT_BITS::M16BITS;
    setting.fifo_sample_rate = FIFO_SAMPLE_RATE::SMPL_200HZ;
    setting.gyro_fchoice = 0x03;
    setting.gyro_dlpf_cfg = GYRO_DLPF_CFG::DLPF_41HZ;
    setting.accel_fchoice = 0x01;
    setting.accel_dlpf_cfg = ACCEL_DLPF_CFG::DLPF_45HZ;
  while(!mpu.setup(0x68,setting,Wire1)) {  // change to your own address
      //Serial.println("MPU connection failed. Please check your connection with `connection_check` example.");
      delay(1000);
      digitalWrite(LED_BUILTIN,!digitalRead(LED_BUILTIN));
  }

  //loadCalibration();
   
  int num =0;
  float tot =0;
  while (num < 1000){
    if (mpu.update()){
      num = num + 1;
      tot = tot + mpu.getGyroZ();
    }
    delay(5);
  }
  offset = tot/num;

  posicionInicial();

  for (int i = 0; i < 10; i++) {
    pixy.changeProg("line");
    delay(100);
  }

  delay(1000);
  digitalWrite(LED_BUILTIN,HIGH);

  while (digitalRead(PIN_BOTON)) {
    /*medirUltrasonidos();
    medirLaseres();
    //distanceTelemetria();
    //EnviarTelemetria();
    delay(100);*/
  }

  //setEnable(1);
  delay(1000);
  setEnable(1);  //*************************************************************************************

  setVelocidad(20);
  //setVelocidad(12);
  //delay(500);     //*******************************************************************
}

void loop() {
  static uint32_t prev_ms_brujula = millis();
  if (mpu.update()) {
    Duracion_de_la_muestra = millis() - prev_ms_brujula;
    prev_ms_brujula = millis();
    valorBrujula = valorBrujula + ((mpu.getGyroZ() - offset) * Duracion_de_la_muestra / 1000);
  }

  static uint32_t prev_ms_posicion = millis();
  if (millis() > prev_ms_posicion) {
    medidaencoder = medirEncoder();
    if (medidaencoder != prev_medidaencoder) {
      double dy = (medidaencoder - prev_medidaencoder) * cos((valorBrujula - 90 * giros) * (M_PI/180));
      double dx = (medidaencoder - prev_medidaencoder) * sin((valorBrujula - 90 * giros) * (M_PI/180));
      prev_medidaencoder = medidaencoder;
      posicionY = posicionY + dy;
      posicionX = posicionX + dx;
      posicionamiento();
    }
    prev_ms_posicion = millis() + 10;
  }


  static uint32_t prev_ms_direccion = millis();
  if (millis() > prev_ms_direccion) {
    ErrorDireccionActual = constrain(ErrorDireccion(valorBrujula - 90 * giros, direccionObjetivo), -127, 127);
    int _setAngle = constrain(servoKP * ErrorDireccionActual + servoKD * (ErrorDireccionActual - ErrorDireccionAnterior), -255, 255);
    if (_setAngle != _setAngleAnterior) {
      if (forward) {
        setGiro(-_setAngle);
      } else {
        setGiro(_setAngle);
      }
      _setAngleAnterior = _setAngle;
    }
    ErrorDireccionAnterior = ErrorDireccionActual;
    prev_ms_direccion = millis() + 10;    
  }
  
  
  static uint32_t prev_ms_ultrasonidos = millis();
  if (millis() > prev_ms_ultrasonidos) {
    prev_ms_ultrasonidos = millis() + 20;
    medirUltrasonidos();
    medirLaseres();
    if (!LecturaGiro) {
      corregirPosicion();
      checkGiro();
      pixy.ccc.getBlocks();
    }
  }

  static uint32_t prev_ms_telemetria = millis();
  if (millis() > prev_ms_telemetria) {
    //EnviarTelemetria();
    //distanceTelemetria();
    posicionTelemetria();
    //Serial.println(medidasLaseres[ultraFrontal]);
    //Serial.println(valorBrujula);
    prev_ms_telemetria = millis() + 30;
  }

  static uint32_t prev_ms_camara = millis();
  if (millis() > prev_ms_camara) {
    prev_ms_camara = millis() + 50;
    if (!LecturaGiro) {
      autoMoverCamara(0);}
    /*if (!LecturaGiro) {
      if (camaraIzquierda == 0) {
        autoMoverCamara(5*14);
      } else if (camaraIzquierda == 4) {
        autoMoverCamara(-5*14);
      }
      camaraIzquierda++;
      if (camaraIzquierda == 8) {
        camaraIzquierda = 0;
      }
    }*/
  }

  

  int mayor = -1;
  int tamano = 0;
  
 switch (estado)
  {
  case e::Inicio:
    if (posicionY > 135 * EncodersPorCM) { 
      setVelocidad(15);
      estado = e::DecidiendoGiro;
    }
  break;

  case e::Recto:
    if ((abs(giros) == 12) && (posicionY >= 120 * EncodersPorCM)) {
      estado = e::Final;
    }
    if (pixy.ccc.numBlocks) {
      for (int i=0; i < pixy.ccc.numBlocks; i++) {
        if (pixy.ccc.blocks[i].m_height > tamano) {
          mayor = i;
          tamano = pixy.ccc.blocks[i].m_height;
        }
      }
    }
    if (tamano > tamanoMinimodeEsquive) {
      if (pixy.ccc.blocks[mayor].m_signature == RedSignature) {
        /*if (posicionY <= 90*EncodersPorCM) {
          if (sentidoGiro) {
            posicionObjetivo = -30 * EncodersPorCM + 5 * EncodersPorCM;
          } else {
            posicionObjetivo = -30 * EncodersPorCM - 5 * EncodersPorCM;
          }
        } else {*/
          posicionObjetivo = -30 * EncodersPorCM;
        //}
      } else if (pixy.ccc.blocks[mayor].m_signature == GreenSignature) {
        /*if (posicionY <= 90*EncodersPorCM) {
          if (sentidoGiro) {
            posicionObjetivo = 30 * EncodersPorCM + 5 * EncodersPorCM;
          } else {
            posicionObjetivo = 30 * EncodersPorCM - 5 * EncodersPorCM;
          }
        } else {*/
          posicionObjetivo = 30 * EncodersPorCM;
        //}
      }
    }
  break;

  case e::DecidiendoGiro:
    pixy.line.getMainFeatures(LINE_VECTOR);
    delay(100);

    pixy.line.numVectors;
    
    if (pixy.line.numVectors) {
      int x0 = pixy.line.vectors[0].m_x0;
      int y0 = pixy.line.vectors[0].m_y0;
      int x1 = pixy.line.vectors[0].m_x1;
      int y1 = pixy.line.vectors[0].m_y1;
      long m = (y1 - y0) * (x1 - x0);
      /* if (m > 0) {
        sentidoGiro = false;
        sentidoParaCorregirPosicion = -1;
        //Serial.println("Sentido false");
      } else if (m < 0) {
        sentidoGiro = true;
        sentidoParaCorregirPosicion = 1;
        //Serial.println("Sentido true");
      } */
      LecturaGiro = false;
      pixy.changeProg("block");
      //setVelocidad(20);
      //setVelocidad(12);
      setVelocidad(25);  //**********************************************************************************
      estado = e::Recto;
    }
  break;

  case e::Final:
    setVelocidad(0);
    setEnable(0);
  break;

 }

}

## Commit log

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2022-06-04 Control de velocidad
    Intento 1. Archivos subidos.
    Cambio de placa a ESP32
2022-06-13 añadido proyecto circuito electrónico
    [Circuito.sch]
2022-06-15 División del código en el Arduino Nano y el ESP32
    Software movida a code
    Creado el proyecto de la ESP32 (ESP Master)
    Creado el proyecto de la arduino Nano (Nano Slave)
2022-06-16 Funcion Corregir Velocidad
    Función Proporcional Diferencial para corregir la velocidad.
    Cambio del Pin Trigger Central (5) al 11 y PinEnMotor (11) a 5, para poder usar el timer2 con el encoder, porque da fallo al estar el motor también en ese timer.
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2022-06-18 Subidos todos los modelos 3D
    [Soporte Bateria-Fillet001.stl, Soporte Bateria.FCStd, Soporte Ultrasonidos.FCStd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]
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2022-06-23 Subir pruebas telemetría.
    [Prueba1.ods, Prueba10.ods, Prueba2.ods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]
2022-06-23 Cuadrado (Bien) & Telemetría
    [Prueba11.ods, Prueba12.ods, Prueba13.ods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]
2022-06-25 Solucion error
    ManiobraIzquierda > ManiobraIzquierda1
    [main.cpp]
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2022-07-07 Correccion del codigo
    Correccion de fallo ( no hacia la maniobra )
2022-07-07 Update de telemetria
    Pruebas 16 y 17
    [Prueba16.ods, Prueba17.ods]
2022-07-09 Subir modelo soporte trasero nuevo
    [Soporte.FCStd, Soporte.stl, Sujetador trasero.FCStd]
2022-07-12 Adición del ultrasonidos trasero
    Cambio del nombre del ultrasonidos central a ultrasonidos frontal en el Nano.
    Creación del ultrasonidos trasero.
2022-07-12 Actualizacion ultrasonidos frontal
    Remplazo de ultraCentral por ultraFrontal.
    Reordenación de algún código
2022-07-13 Creacion del ultrasonidos trasero (Obstaculos)
    Creacion del ultrasonidos trasero.
    ultraCentral >>>>> ultraFrontal.
    Supresion de codigo inutil.
    Reordenacion de codigo.
2022-07-14 Cambio de pines
    Pin Trigger Trasero: A6 >>> D13.
    Pin Echo Trasero: A7 >>> A1.
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2022-07-21 Nuevas pruebas
    [Prueba19.ods, Prueba20.ods, Prueba21.ods]
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2022-08-02 Intento correccion de fallos
    (Al iniciar los ultra son 0, fallos en la maniobra...)
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2022-08-04 Deteccion de giro por lineas
    Hay algunos errores
    [main.cpp]
2022-09-05 Solucion fallos arranque
    Al incorporar las luces iniciales, el coche al arrancar daba marcha atrás.
2022-09-05 cambio de nombre
    telemetría > telemetry
    [Prueba1.ods, Prueba10.ods, Prueba11.ods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]
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2022-09-06 Detección Giro Líneas
    Corrección de error ( Se movía a trompicones)
    + Prueba sistema de detección del sentido de giro finalizada
    [components.h, main.cpp]
2022-09-07 Telemetria subida
    Prueba 22 ( Lectura de las lineas)
    [Prueba22.ods]
2022-09-07 Telemetria Pruebas 22 y 23
    Pruebas de reconocimiento de lineas
    [Prueba22.ods, Prueba23.ods]
2022-09-09 Rename
    Programa para probar las lineas (renamed)
    Programa para probar la maniobra (created)
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2022-09-12 Unificación del esquive de bloques
    Esquivar derecha y esquivar izquierda -> Esquivar
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2022-09-13 Estado final establecido
    Ahora el coche se para en la tercera vuelta.
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2022-09-14 Update of MapSaving & MapLoading
    Map Saving ahora almacena los principales valores de cada bloque.
    Map Loading detecta cuando solo hay un bloque en un cierto tramo
2022-09-14 Solución problema
    Reconocimiento de giro fallaba cuando el vector tenia el sentido opuesto
    [main.cpp]
2022-09-14 Maniobra centrar
    Hecha la maniobra de centrado despues del esquive de los bloques
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2022-09-23 Programa Bluetooth
    Programa para la plaquita Arduino Uno para que funcione el Bluetooth.
2022-09-24 Update de estados Map Loading
    Correccion de algunos fallos
    Mejora de codigo
    Anotaciones
2022-09-29 Modelos 3D
    Subir los modelos nuevos a sus respectivas carpetas, y una actulización del README.md de la carpeta "models".
    [Soporte delantero-Cut002.stl, Soporte delantero-Cut002Tumbado.stl, Soporte delantero.FCStd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]
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2022-10-29 Rastreador de posicion V1
    Algoritmo para saber la posicion del coche V1
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2022-11-03 03/11/2022 V1
    Obtencion de la posicion del coche (aproxiamdo).
    Copia de la antigua version del master obstaculos. (Checkpoint)
2022-11-03 03/11/2022 V2
    Update en telemetry (Readme creado).
    Nuevos componentes (Color & Laser).
2022-11-05 05/11/2022 V1
    Detectar la posicion inicial del coche.
    Medir los ultrasonidos en el setup.
    Actualizacion de los schemes.
2022-11-05 05/11/2022 v2
    Modelos 3D subidos
    Correccion de errores fase 1
    Inicio con deteccion de posicion fase 2
    [Soporte Frontal.stl, Soporte camara - Base servo.stl, Soporte camara - Camara_1.stl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]
2022-11-08 Nano Slave 2
    Nuevo Codigo para el Arduino Nano Every (como Slave).
    Medicion de distancia por TOF.
2022-11-09 09/11/2022 V1
    Nano Slave 2 I2C functions created.
    Correccion en la libreria components.h de Nano Slave 1.
    Reordenacion de algunas variables en el Nano Slave.
    Incluida la libreria ESP32Servo a ESP32 Master Obstaculos.
    Creada la funcion de obtencion de posicion.
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2022-11-10 10/11/2022 V1
    Correccion Nano Slave 2.
    Funcion Mover camara.
    Sistema de coordenadas ahora siempre tiene el negativo de las X en la pared.
    Skecth de Esquivar Derecha 2.
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2022-11-12 Add files via upload
    Circuito 2.1
    [Circuito.sch]
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2022-11-15 Medidas laseres Fase 1
    Incluido el codigo de medir laseres al ESP32 de la fase 1.
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2022-11-15 Map Recon V2.1
    Solution to the -1th lap problem.
    [main.cpp]
2022-11-16 Colors update
    Funcion para hacer la rotacion de colores.
    Update en la verification list.
2022-11-16 Documentation Updated
    [Prueba1.ods, Prueba10.ods, Prueba11.ods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]
2022-11-17 El diagrama del codigo
    No es un buen trabajo, pero es lo que hay.
2022-11-20 Todo lo de la competición
    Los cambios hecos durante estos tres días.
